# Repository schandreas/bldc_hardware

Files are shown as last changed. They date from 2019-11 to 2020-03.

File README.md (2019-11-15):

This is a fork of Benjamin Vedders Open Source VESC project: https://github.com/vedderb/bldc-hardware

## Goals: 
The original Vesc design is very good for the things it wants to do. I want to do different things and still be able to use the same firmware. So I made this version.

The idea was that I only wanted to drive very weak motors. So this version is cheap and not that good. :man_shrugging:

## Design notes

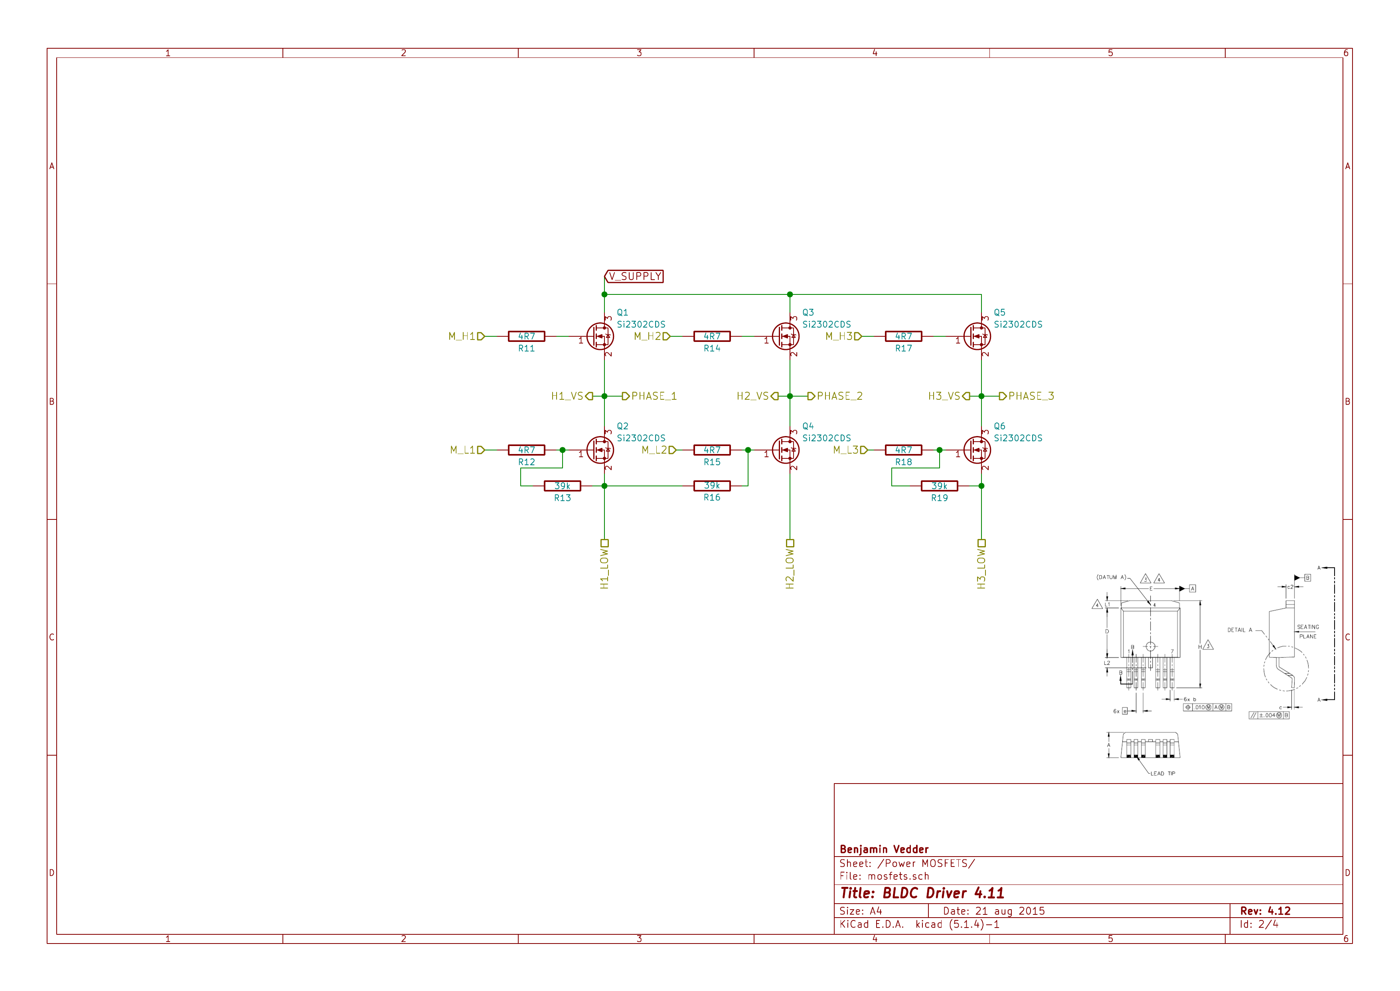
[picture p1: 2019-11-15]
design/PNGs/Schematic-2.png

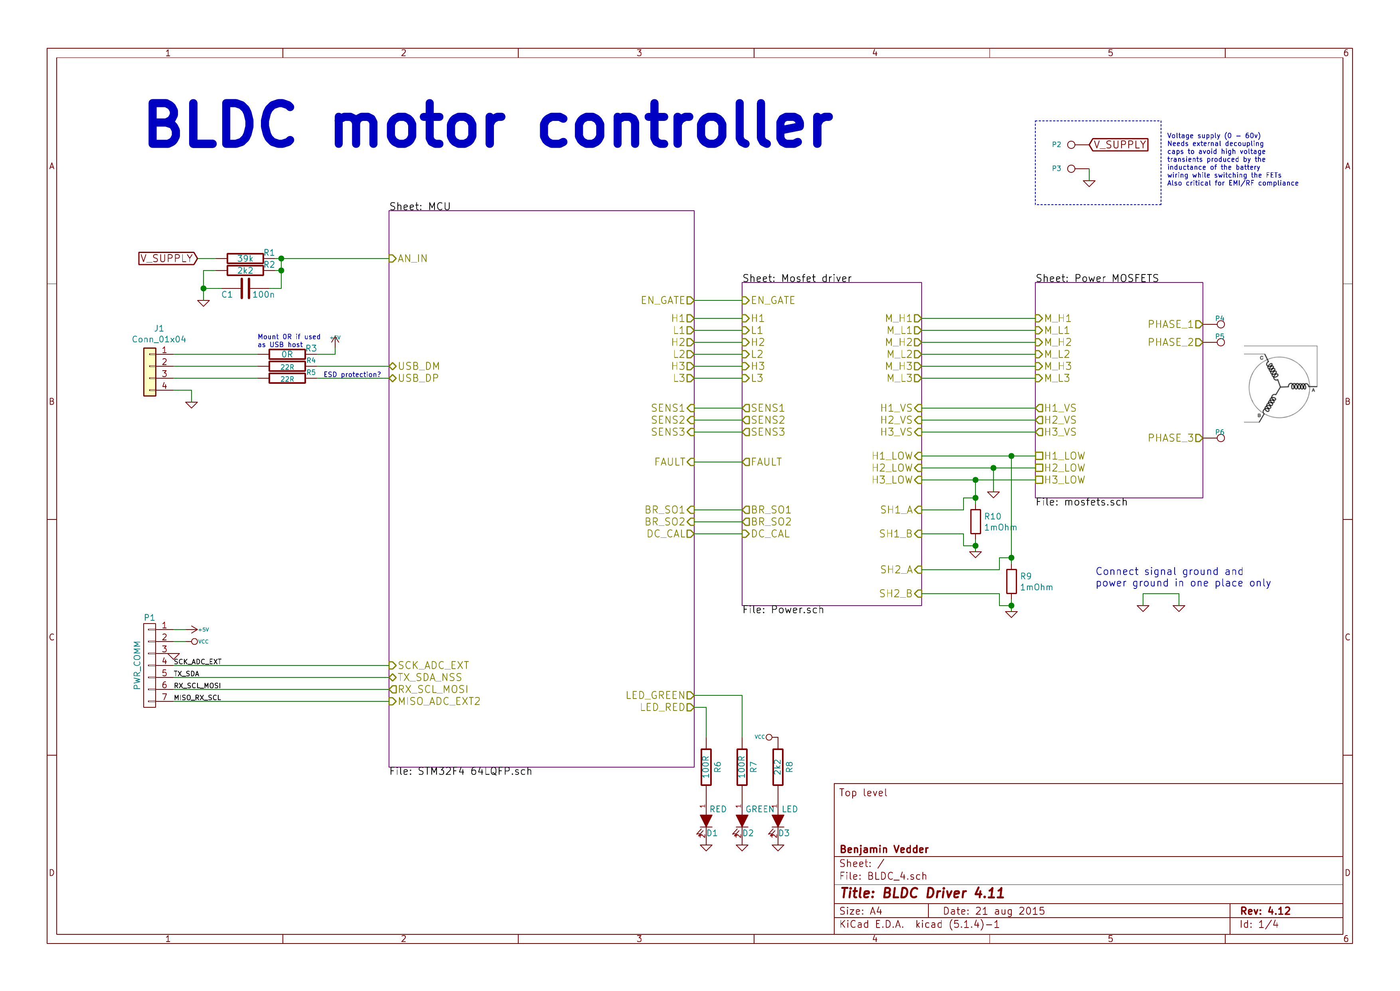
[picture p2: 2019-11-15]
design/PNGs/Schematic-1.png

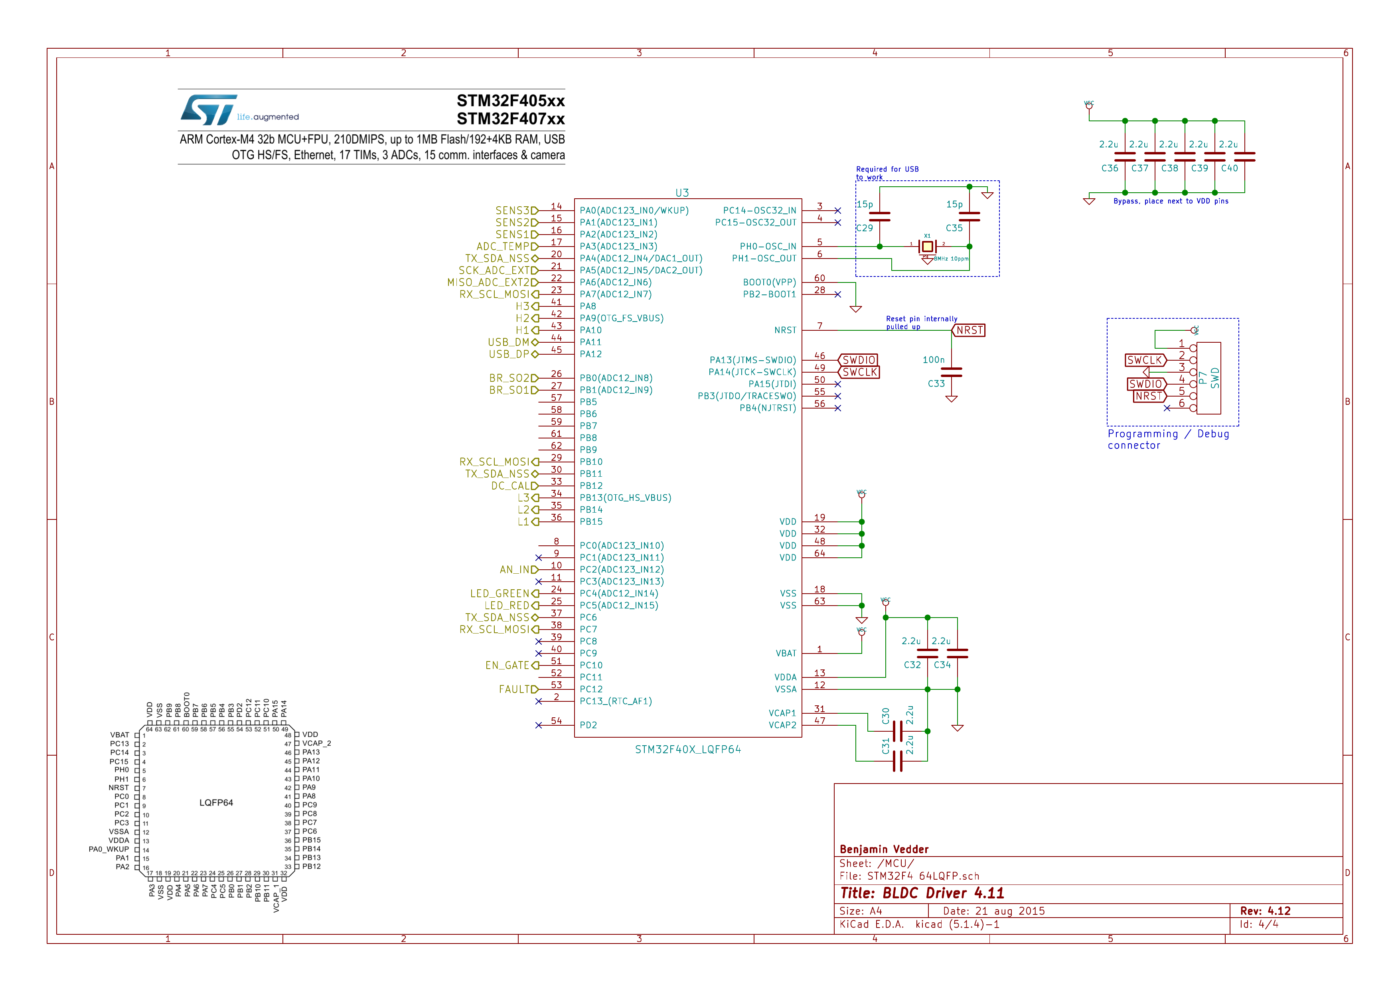
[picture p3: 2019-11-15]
design/PNGs/Schematic-4.png

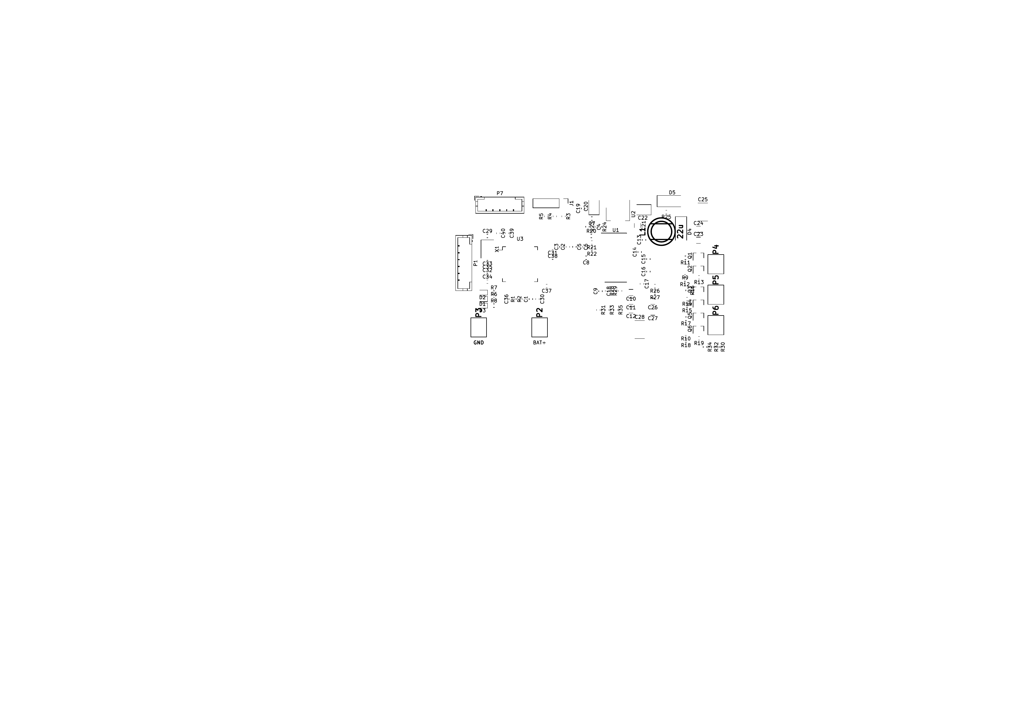
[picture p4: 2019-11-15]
design/PNGs/F_Modules-1.png

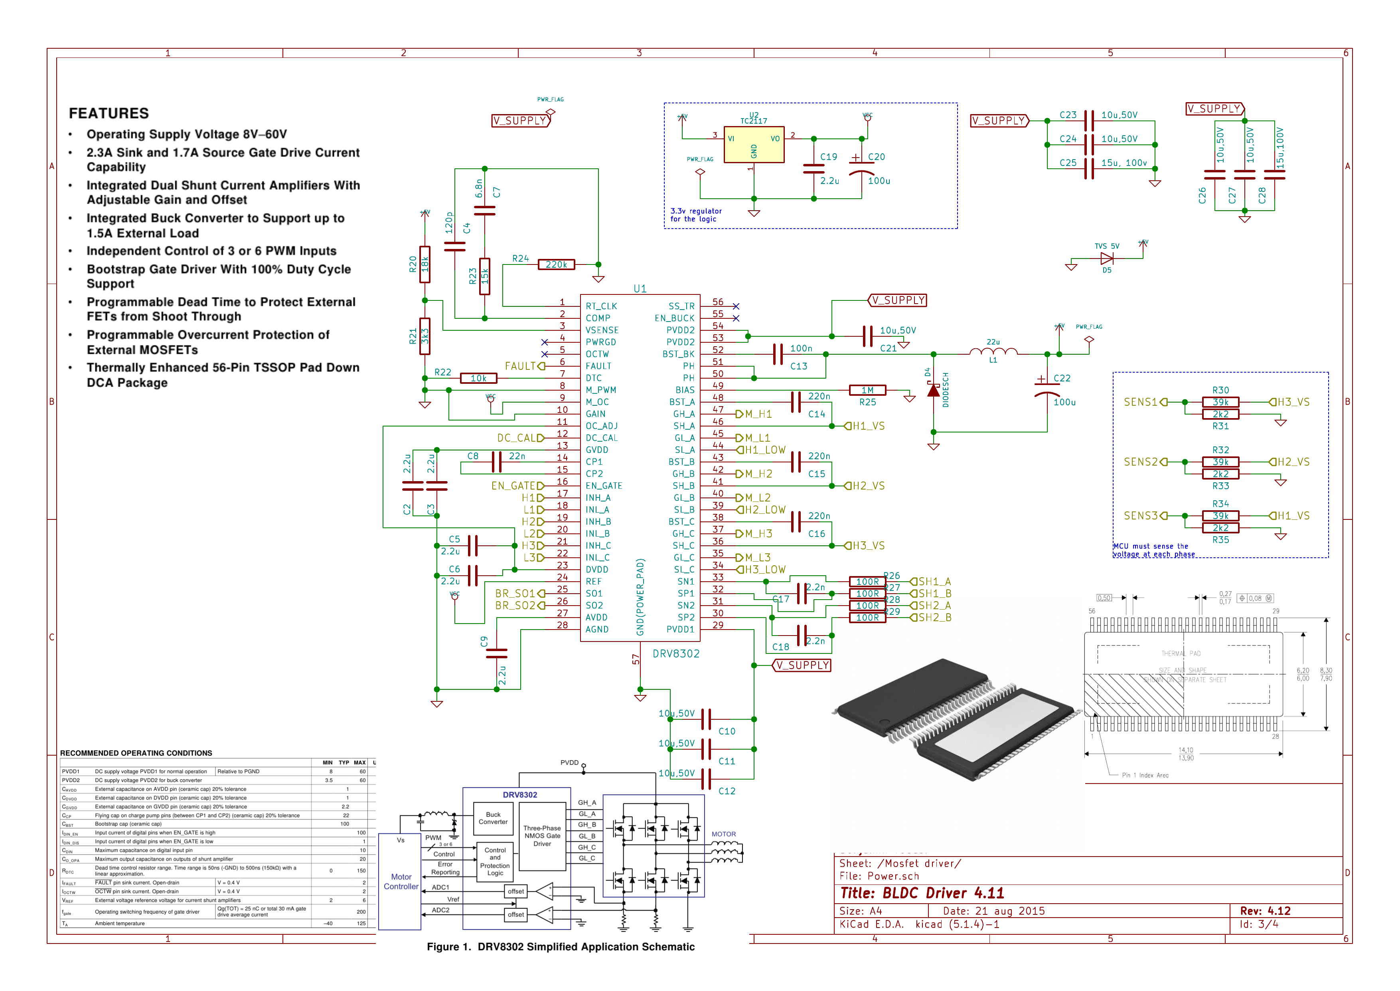
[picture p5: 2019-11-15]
design/PNGs/Schematic-3.png

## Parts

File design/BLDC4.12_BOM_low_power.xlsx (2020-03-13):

Part | Value | Package | Description | Qty | Place (YES/NO) | Distributor | Order Number | Comment | single price | multi price | link | LCSC
U1 |  | LQFP-64 | STM32F405RGT6 MCU | 1 | YES | RS | 746-8217 |  | 9.24 € | 9.24 € | https://at.rs-online.com/web/p/mikrocontroller/7468217/ | https://lcsc.com/product-detail/ST-Microelectronics_STMicroelectronics_STM32F405RGT6_STM32F405RGT6_C15742.html
U2 |  | SOT-223-3 | VREG | 1 | YES | RS | 823-4434 | moq 10 | 0.63 € | 0.63 € | https://at.rs-online.com/web/p/ldo-spannungsregler/8234434/ | https://lcsc.com/product-detail/Low-Dropout-Regulators-LDO_MICROCHIP_TC2117-3-3VDBTR_TC2117-3-3VDBTR_C98655.html
U3 |  | HTSSOP-56-PP | MOSFET Driver | 1 | YES | RS | 762-0421 |  | 5.45 € | 5.45 € | https://at.rs-online.com/web/p/motor-treiber-ics/7620421/ | https://lcsc.com/product-detail/MOS-Drivers_TI_DRV8302DCA_DRV8302DCA_C84672.html
L1 |  | inductor_smd_8x5mm | Power Inductor | 1 | YES | MOUSER | 652-SDR0805-220ML |  | 0.45 € | 0.45 € | https://www.mouser.at/ProductDetail/Bourns/SDR0805-220ML
X1 |  | Conn_1x04 | Pinheader 1x04 2.54mm | 1 | YES | RS | 720-1310 | moq 10 | 0.23 € | 0.23 € | https://at.rs-online.com/web/p/leiterplatten-header/7201310/?sra=pstk
X2 | 8MHz | Crystal_5x3mm | Crystal 8MHz, 10PPM | 1 | YES | MOUSER | 815-ABM3B-8.0-10-1UT |  | 0.62 € | 0.62 € | https://www.mouser.at/ProductDetail/ABRACON/ABM3B-8000MHZ-10-1UT | https://lcsc.com/product-detail/Power-Inductors_BOURNS_SDR0805-220ML_BOURNS-SDR0805-220ML_C139488.html
Q1-Q6 | Si2302CDS | SOT-23 | MOSFET 20V 3A | 6 | YES | Farnell | 1684049 |  | 0.19 € | 1.15 € | https://at.farnell.com/vishay/si2302cds-t1-ge3/mosfet-n-kanal-sot-23/dp/1684049?st=Si2302CDS
R53,R54 | 25mOhm | SMD-0612 | Shunt 25mOhm | 2 | YES | MOUSER | 660-WU732B15TTD25L0F |  | 0.53 € | 1.06 € | https://www.mouser.at/ProductDetail/KOA-Speer/WU732B15TTD25L0F
D5 | 5V | DO-214AC-2 | TVS diode 5V | 1 | YES | MOUSER | 576-SMAJ5.0A |  | 0.37 € | 0.37 € | https://www.mouser.at/ProductDetail/Littelfuse/SMAJ50A
D4 | 60V 2A | SOD-123W-2 | Shottky 60V 2A | 1 | YES | MOUSER | 771-PMEG6020ER-115 | Voltage and current important | 0.32 € | 0.32 € | https://www.mouser.at/ProductDetail/Nexperia/PMEG6020ER115
C25,C33 | 100uF, 6.3V | c_tant_B | CAP 100u, 6.3V | 2 | YES | RS | 136-4122 | Voltage important, moq 25 | 0.44 € | 0.88 € | https://at.rs-online.com/web/p/tantal-elektrolytkondensator/1364122/
C1,C8,C9,C39,C40,C43,C44,C49 | 10uF 50V | SMD1206 | CAP 10u, 50V, 1206 | 8 | YES | MOUSER | 963-UMK316BBJ106ML-T | Voltage important, moq 10 | 0.31 € | 2.48 € | https://www.mouser.at/ProductDetail/Taiyo-Yuden/UMK316BBJ106ML-T
C37,C51 | 15uF, 100V | SMD-2220 | CAP 15u, 100V, 2220 | 2 | YES | MOUSER | 810-CGA9P3X7S2A156M | Voltage important | 3.24 € | 6.48 € | https://www.mouser.at/ProductDetail/TDK/CGA9P3X7S2A156M250KB
C2,C27,C32 | 100nF, 50V | SMD-0603 | CAP 100n, 50V, 0603 | 3 | YES | MOUSER | 581-06035C104JAT2A | Voltage important | 0.14 € | 0.41 € | https://www.mouser.at/ProductDetail/AVX/06035C104JAT2A
C28,C29,C30 | 220nF,25V | SMD-0603 | CAP 220n, 25V, 0603 | 3 | YES | MOUSER | 963-TMK107B7224KA-T | Voltage important | 0.10 € | 0.30 € | https://www.mouser.at/ProductDetail/Taiyo-Yuden/TMK107B7224KA-T
C24,C10,C11,C12,C13,C14,C16,C17,C18,C20,C23,C26,C31,C35,C52 | 2.2uF, 16V | SMD-0603 | CAP 2.2u, 16V, 0603 | 15 | YES | MOUSER | 810-C1608X5R1C225M | Voltage important, moq 10 | 0.17 € | 2.57 € | https://www.mouser.at/ProductDetail/TDK/C1608X5R1C225M080AB
P3 |  | MICRO_JST_7 | Micro-JST 7PIN 2mm | 1 | YES | Conrad | 740103 - 62 | Can be found on ebay (http://www.ebay.com/sch/i.html?_odkw=jst+6+pin+2.0&_osacat=0&_from=R40&_nkw=jst+7+pin+2.0&_sacat=0) | 0.44 € | 0.44 € | https://www.conrad.at/de/p/jst-einbau-stiftleiste-standard-ph-polzahl-gesamt-7-rastermass-2-mm-b7b-ph-k-s-lf-sn-1-st-740103.html | https://lcsc.com/product-detail/Wire-To-Board-Wire-To-Wire-Connector_JST-Sales-America_B7B-PH-K-S-LF-SN_JST-Sales-America-B7B-PH-K-S-LF-SN_C157981.html
P2 |  | MICRO_JST_6 | Micro-JST 6PIN 2mm | 1 | YES | Conrad | 741271 - 62 | Can be found on ebay (http://www.ebay.com/sch/i.html?_odkw=jst+7+pin+2.0&_osacat=0&_from=R40&_nkw=jst+6+pin+2.0&_sacat=0) | 0.69 € | 0.69 € | https://www.conrad.at/de/p/jst-einbau-stiftleiste-standard-ph-polzahl-gesamt-6-rastermass-2-mm-b6b-ph-k-s-lf-sn-1-st-741271.html | https://lcsc.com/product-detail/Wire-To-Board-Wire-To-Wire-Connector_JST-Sales-America_B6B-PH-K-S-LF-SN_JST-Sales-America-B6B-PH-K-S-LF-SN_C131342.html
C34, C36 | 2.2nF, 50V | SMD-0603 | CAP 2.2n, 50V, 0603 | 2 | YES | Farnell | 2409039 | moq 10 | 0.04 € | 0.08 € | https://at.farnell.com/kemet/c0603c222j5ractu/kondensator-2200pf-50v-5-x7r-0603/dp/2409039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 | https://lcsc.com/product-detail/Multilayer-Ceramic-Capacitors-MLCC-SMD-SMT_muRata_GRM188R71H222KA01D_2-2nF-222-10-50V_C86023.html
C15,C38 | 15pF, 100V | SMD-0603 | CAP 15p, 100V, 0603 | 2 | YES | MOUSER | 81-GRM1885C2A150JA01 |  | 0.10 € | 0.20 € | https://www.mouser.at/ProductDetail/Murata-Electronics/GRM1885C2A150JA01D | https://lcsc.com/product-detail/Multilayer-Ceramic-Capacitors-MLCC-SMD-SMT_muRata_GRM1885C2A150JA01D_15pF-150-5-100V_C97715.html
C19 | 120pF, 50V | SMD-0603 | CAP 120p, 50V, 0603 | 1 | YES | MOUSER | 81-GRM39C121J50 |  | 0.14 € | 0.14 € | https://www.mouser.at/ProductDetail/Murata-Electronics/GRM1885C1H121JA01J | https://lcsc.com/product-detail/Multilayer-Ceramic-Capacitors-MLCC-SMD-SMT_Murata-Electronics-GRM1885C1H101JA01J_C415381.html
C21 | 6.8nF, 50V | SMD-0603 | CAP 6.8n, 50V, 0603 | 1 | YES | Farnell | 1759100 | moq 10 | 0.01 € | 0.01 € | https://at.farnell.com/multicomp/mc0603b682k500ct/kondensator-6800pf-50v-10-x7r/dp/1759100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 | https://lcsc.com/product-detail/Multilayer-Ceramic-Capacitors-MLCC-SMD-SMT_MuRata_GRM188R71H682KA01D_6-8nF-682-10-50V_C97896.html
C22 | 22nF, 50V | SMD-0603 | CAP 22n, 50V, 0603 | 1 | YES | Farnell | 1414625 | moq 10 | 0.05 € | 0.05 € | https://at.farnell.com/kemet/c0603c223k5ractu/kondensator-0-022-f-50v-10-x7r/dp/1414625?st=C0603C223K5RACTU | https://lcsc.com/product-detail/Multilayer-Ceramic-Capacitors-MLCC-SMD-SMT_KEMET_C0603C223K5RAC7867_22nF-223-10-50V_C141095.html
D1 |  | SMD-0603 | LED Green, 0603 | 1 | YES | MOUSER | 859-LTST-C191KGKT |  | 0.23 € | 0.23 € | https://www.mouser.at/ProductDetail/Lite-On/LTST-C191KGKT | https://lcsc.com/product-detail/Light-Emitting-Diodes-LED_SMD-green_C125098.html
D2 |  | SMD-0603 | LED Red, 0603 | 1 | YES | MOUSER | 859-LTST-C191KRKT |  | 0.23 € | 0.23 € | https://www.mouser.at/ProductDetail/Lite-On/LTST-C191KRKT | https://lcsc.com/product-detail/Light-Emitting-Diodes-LED_SMD-red_C125099.html
D3 |  | SMD-0603 | LED Blue, 0603 | 1 | YES | MOUSER | 720-LBQ39GN1P1351 |  | 0.39 € | 0.39 € | https://www.mouser.at/ProductDetail/OSRAM-Opto-Semiconductors/LB-Q39G-N1OO-35-1
R28,R29,R34,R35,R42,R43 | 4.7ohm | SMD-0603 | R 4.7ohm, 0603 | 6 | YES | MOUSER | 660-RK73H1JTTD4R70F | moq 10 | 0.02 € | 0.13 € | https://www.mouser.at/ProductDetail/KOA-Speer/RK73H1JTTD4R70F | https://lcsc.com/product-detail/Chip-Resistor-Surface-Mount_KOA-Speer-Elec-RK73H1JTTD4R70F_C211717.html
R37,R38,R48-R51,R401 | 100ohm | SMD-0603 | R 100ohm, 0603 | 6 | YES | Farnell | 2074165 | moq 10 | 0.01 € | 0.06 € | https://at.farnell.com/multicomp/mcsr06x1000ftl/keramikwiderstand-100r-1-0-1w/dp/2074165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 | https://lcsc.com/product-detail/Chip-Resistor-Surface-Mount_100R-100R-1_C139043.html
R4,R5,R11,R12,R13,R22,R24,R27,R33 | 2.2kOhm | SMD-0603 | R 2.2k, 0603 | 5 | YES | Farnell | 2074215 | moq 10 | 0.01 € | 0.05 € | https://at.farnell.com/multicomp/mcsr06x2201ftl/keramikwiderstand-2k2-1-0-1w-0603/dp/2074215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 | https://lcsc.com/product-detail/Chip-Resistor-Surface-Mount_2-2KR-2201-1_C130233.html
R18 | 3.3kOhm | SMD-0603 | R 3.3k, 0603 | 1 | YES | MOUSER | 660-RK73H1JTTD3301F |  | 0.10 € | 0.10 € | https://www.mouser.at/ProductDetail/KOA-Speer/RK73H1JTTD3301F | https://lcsc.com/product-detail/Chip-Resistor-Surface-Mount_3-3KR-3301-1_C160039.html
R20 | 10kOhm | SMD-0603 | R 10k, 0603 | 1 | YES | Farnell | 2074167 | moq 10 | 0.01 € | 0.01 € | https://at.farnell.com/multicomp/mcsr06x1002ftl/keramikwiderstand-10k-1-0-1w-0603/dp/2074167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 | https://lcsc.com/product-detail/Chip-Resistor-Surface-Mount_10KR-1002-1_C130232.html
R19 | 15kOhm | SMD-0603 | R 15k, 0603 | 1 | YES | MOUSER | 660-RK73H1JTTD1502F |  | 0.10 € | 0.10 € | https://www.mouser.at/ProductDetail/KOA-Speer/RK73H1JTTD1502F | https://lcsc.com/product-detail/Chip-Resistor-Surface-Mount_15KR-1502-1_C160018.html
R17 | 18kOhm | SMD-0603 | R 18k, 0603 | 1 | YES | Farnell | 2074204 |  | 0.01 € | 0.01 € | https://at.farnell.com/multicomp/mcsr06x1802ftl/keramikwiderstand-18k-1-0-1w-0603/dp/2074204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 | https://lcsc.com/product-detail/Chip-Resistor-Surface-Mount_18KR-1802-1_C211701.html
R3,R23,R26,R30,R32,R36,R46 | 39kOhm | SMD-0603 | R 39k, 0603 | 7 | YES | Farnell | 2303209 | moq 10 | 0.02 € | 0.11 € | https://at.farnell.com/panasonic/erj3ekf3902v/dickschichtwiderstand-39k-1-100mw/dp/2303209?st=ERJ-3EKF3902V | https://lcsc.com/product-detail/Chip-Resistor-Surface-Mount_PANASONIC-ERJ3EKF3902V_C278624.html
R21 | 220kOhm | SMD-0603 | R 220k, 0603 | 1 | YES | MOUSER | 660-RK73H1JTTD2203F |  | 0.10 € | 0.10 € | https://www.mouser.at/ProductDetail/KOA-Speer/RK73H1JTTD2203F | https://lcsc.com/product-detail/Others_KOA-Speer-Elec-RK73H1JTTD2203F_C268814.html
R25 | 1MOhm | SMD-0603 | R 1M, 0603 | 1 | YES | MOUSER | 660-RK73H1JTTD1004F |  | 0.10 € | 0.10 € | https://www.mouser.at/ProductDetail/KOA-Speer/RK73H1JTTD1004F | https://lcsc.com/product-detail/Chip-Resistor-Surface-Mount_1MR-1004-1_C139051.html
R103, R104 | 22ohm | SMD-0603 | R 22R, 0603 | 2 | YES | Farnell | 2074219 | moq 10 | 0.01 € | 0.03 € | https://at.farnell.com/multicomp/mcsr06x22r0ftl/keramikwiderstand-22r-1-0-1w-0603/dp/2074219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 | https://lcsc.com/product-detail/Chip-Resistor-Surface-Mount_22R-22R0-1_C160030.html
R6 |  |  |  | 0 | NO |  |  | Do not mount |  | 0.00 €
1PIN,1PIN |  |  |  | 0 | NO |  |  | Do not mount |  | 0.00 €
K1 |  |  |  | 0 | NO |  |  | Do not mount |  | 0.00 €
P5,P5,P6,P7,P9 |  |  |  | 0 | NO |  |  | Do not mount |  | 0.00 €
G*** |  |  |  | 0 | NO |  |  | Do not mount |  | 0.00 €
 |  |  |  |  |  |  |  |  |  | 35.88 €
 |  |  |  | 20 |  | RS | · 820-1412 | moq 10-40 | 0.60 € |  | https://at.rs-online.com/web/p/konfektionierte-automationskabel/8201412/
 |  |  |  | 10 |  | RS | · 820-1481 | moq 10-490 | 0.10 € |  | https://at.rs-online.com/web/p/leiterplattensteckverbinder-gehause/8201481/
 |  |  |  | 10 |  | RS | · 820-1478 | moq 10-490 | 0.08 € |  | https://at.rs-online.com/web/p/leiterplattensteckverbinder-gehause/8201478/
 |  |  |  | 100 |  | RS | · 820-1456 | moq 100-900 | 0.03 € |  | https://at.rs-online.com/web/p/kontakte-fur-leiterplattensteckverbinder/8201456/

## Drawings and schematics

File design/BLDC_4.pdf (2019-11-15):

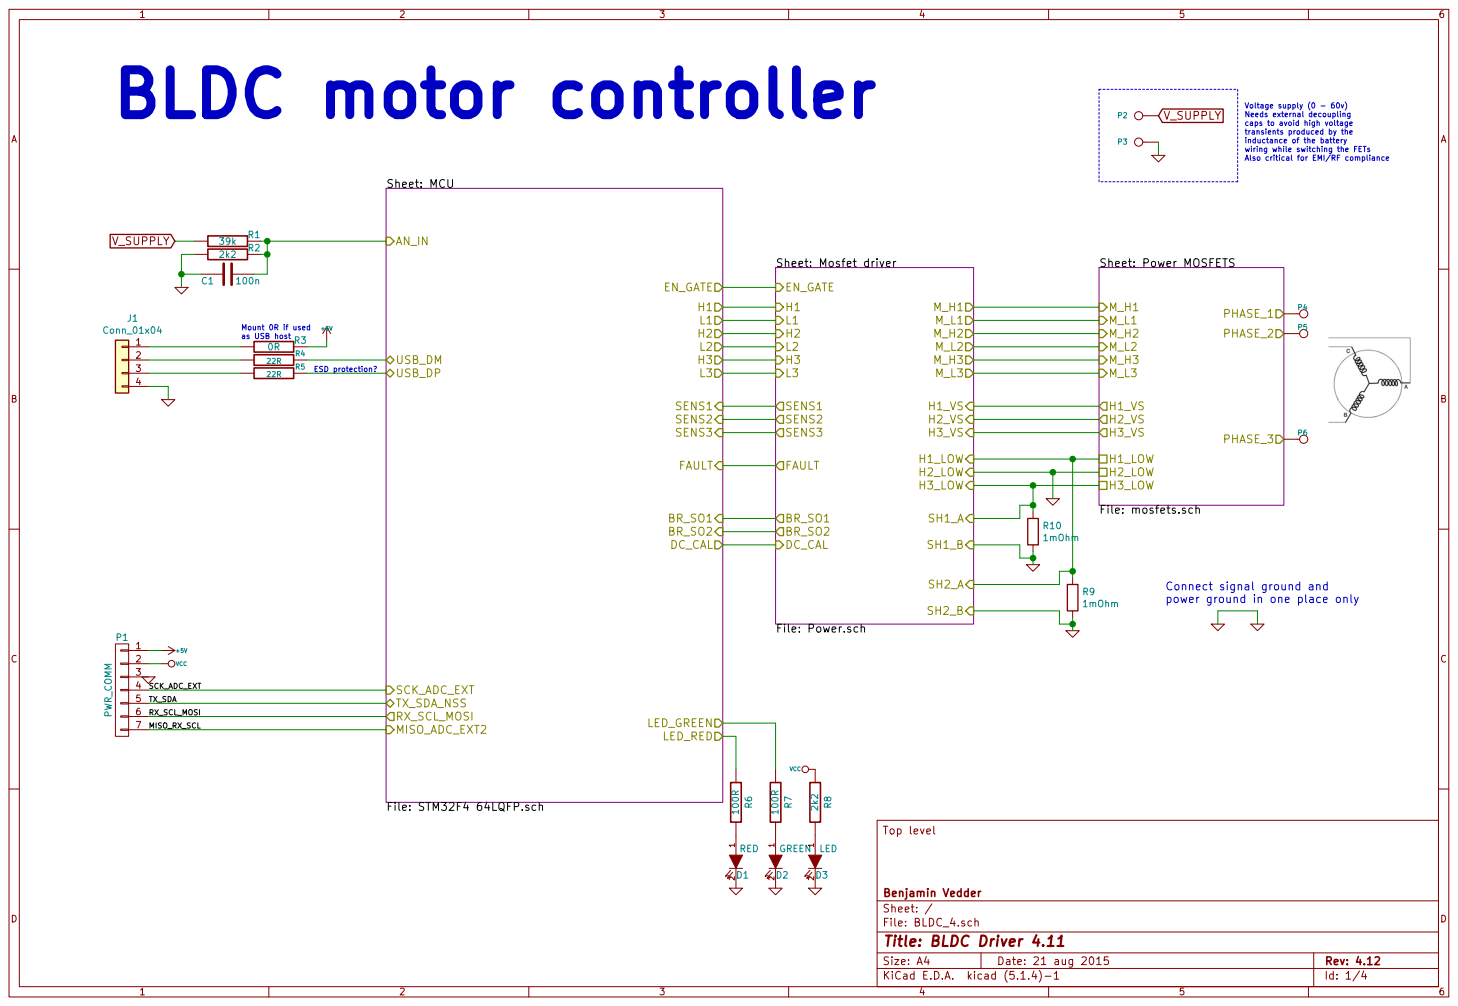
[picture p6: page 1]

inductance of the battery wiring while switching the FETs Also critical for EMI/RF compliance BLDC motor controller

Voltage supply (0 - 60v) Needs external decoupling

caps to avoid high voltage
transients produced by the

ESD protection? Mount 0R if used

power ground in one place only

File: BLDC_4.sch Sheet: / Benjamin Vedder

Id: 1/4 Title: BLDC Driver 4.11

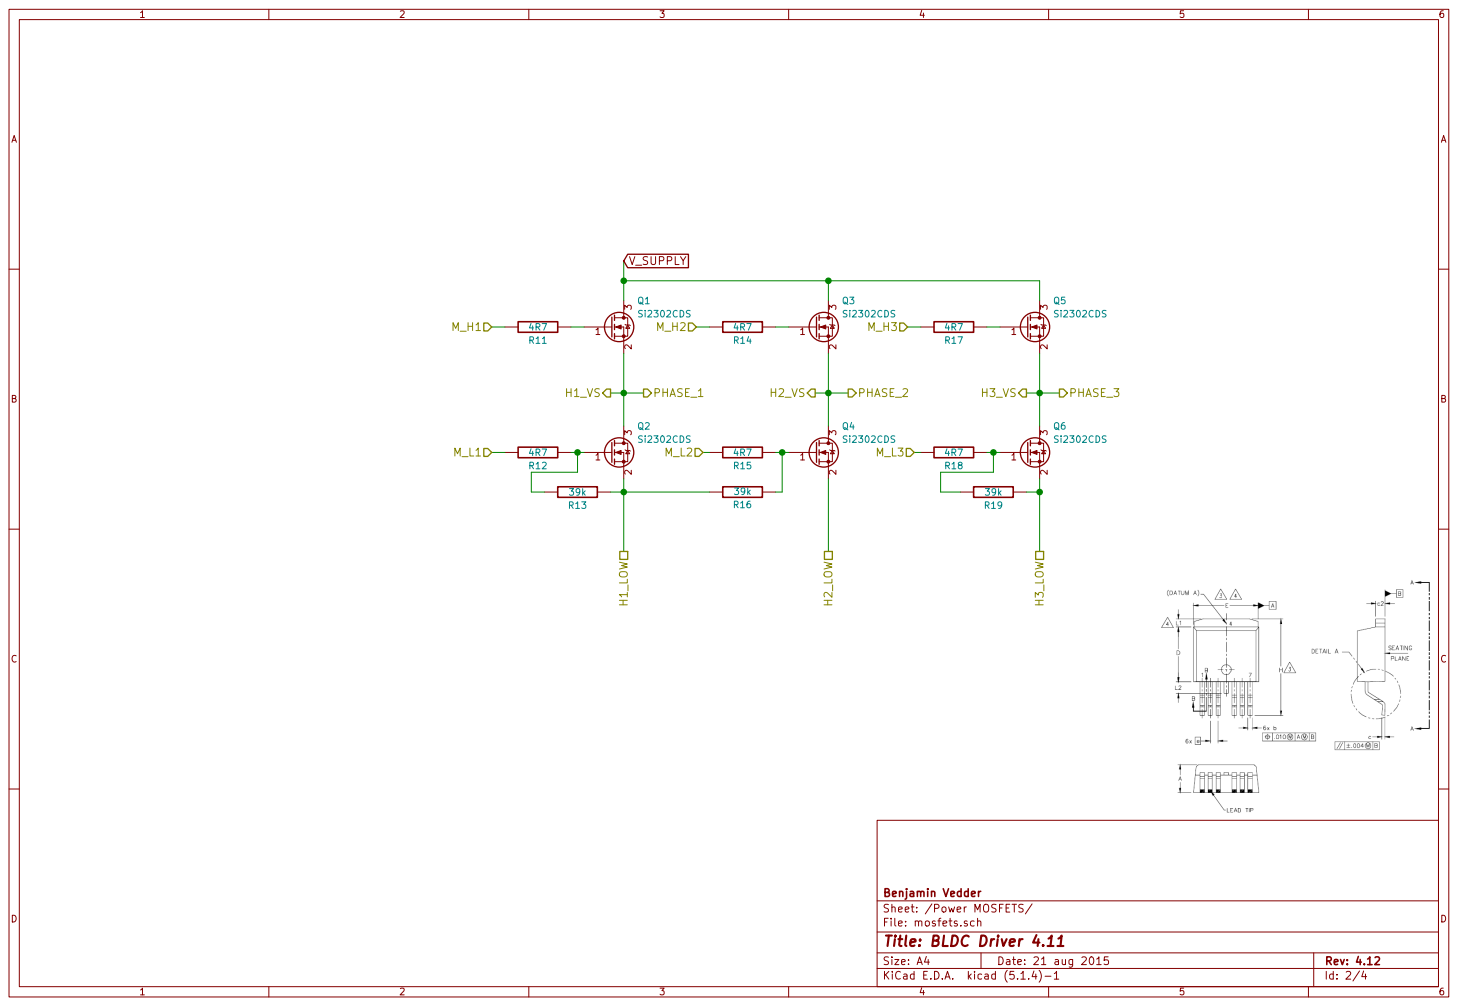
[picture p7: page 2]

File: mosfets.sch Sheet: /Power MOSFETS/ Benjamin Vedder R13

Id: 2/4 Title: BLDC Driver 4.11

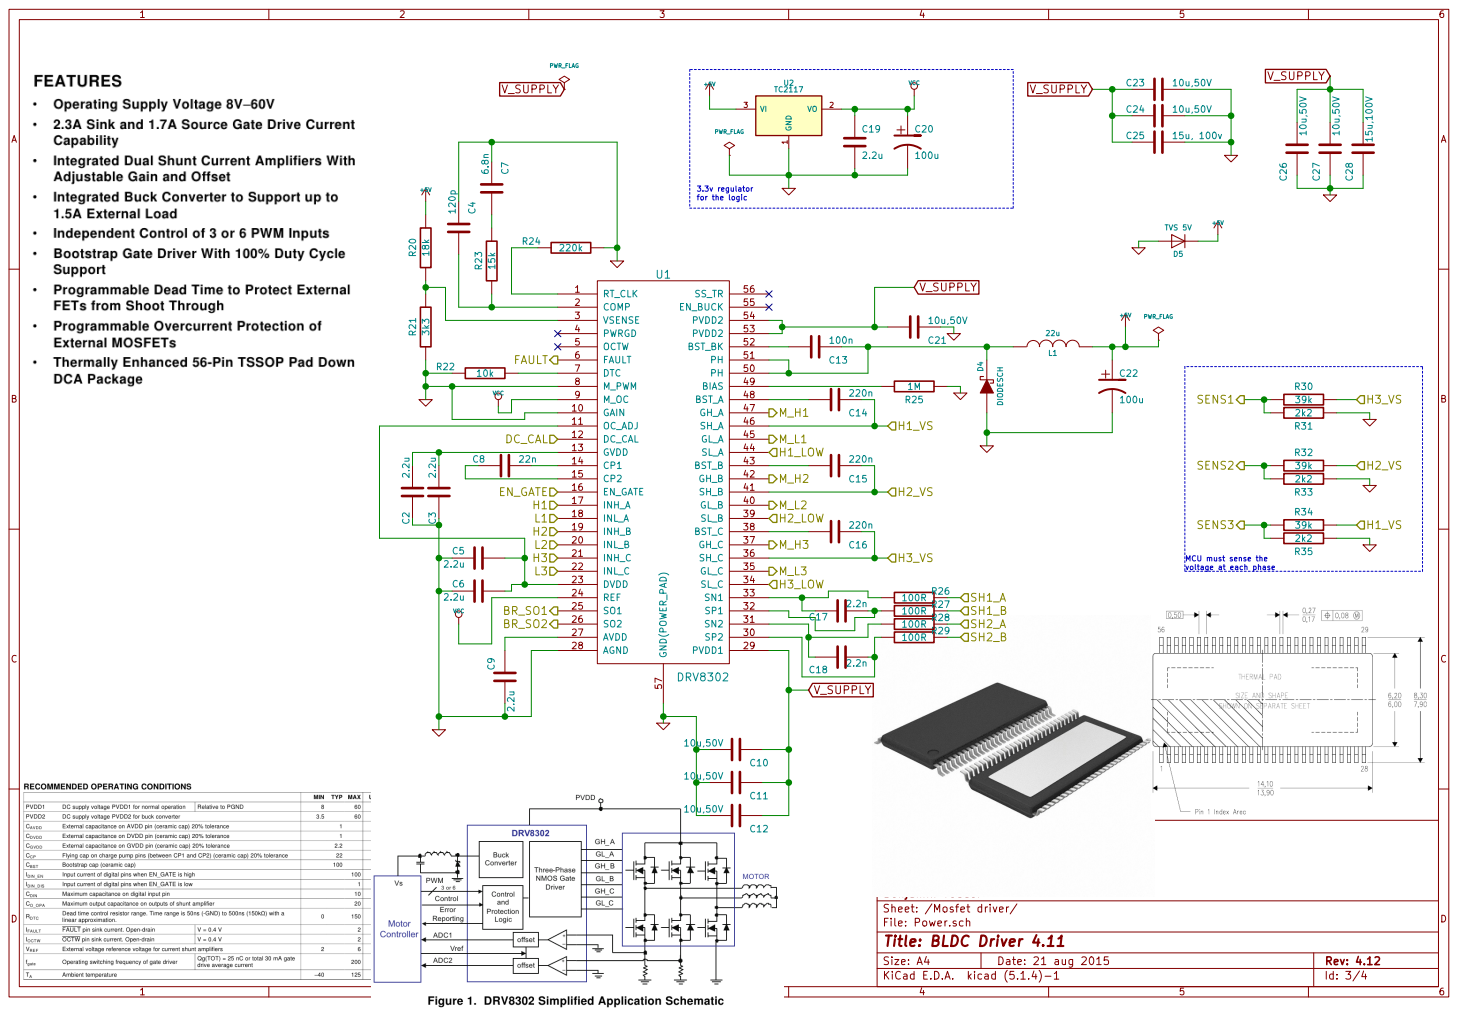
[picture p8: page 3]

MCU must sense the
voltage at each phase

File: Power.sch Sheet: /Mosfet driver/ Benjamin Vedder

Id: 3/4 Title: BLDC Driver 4.11

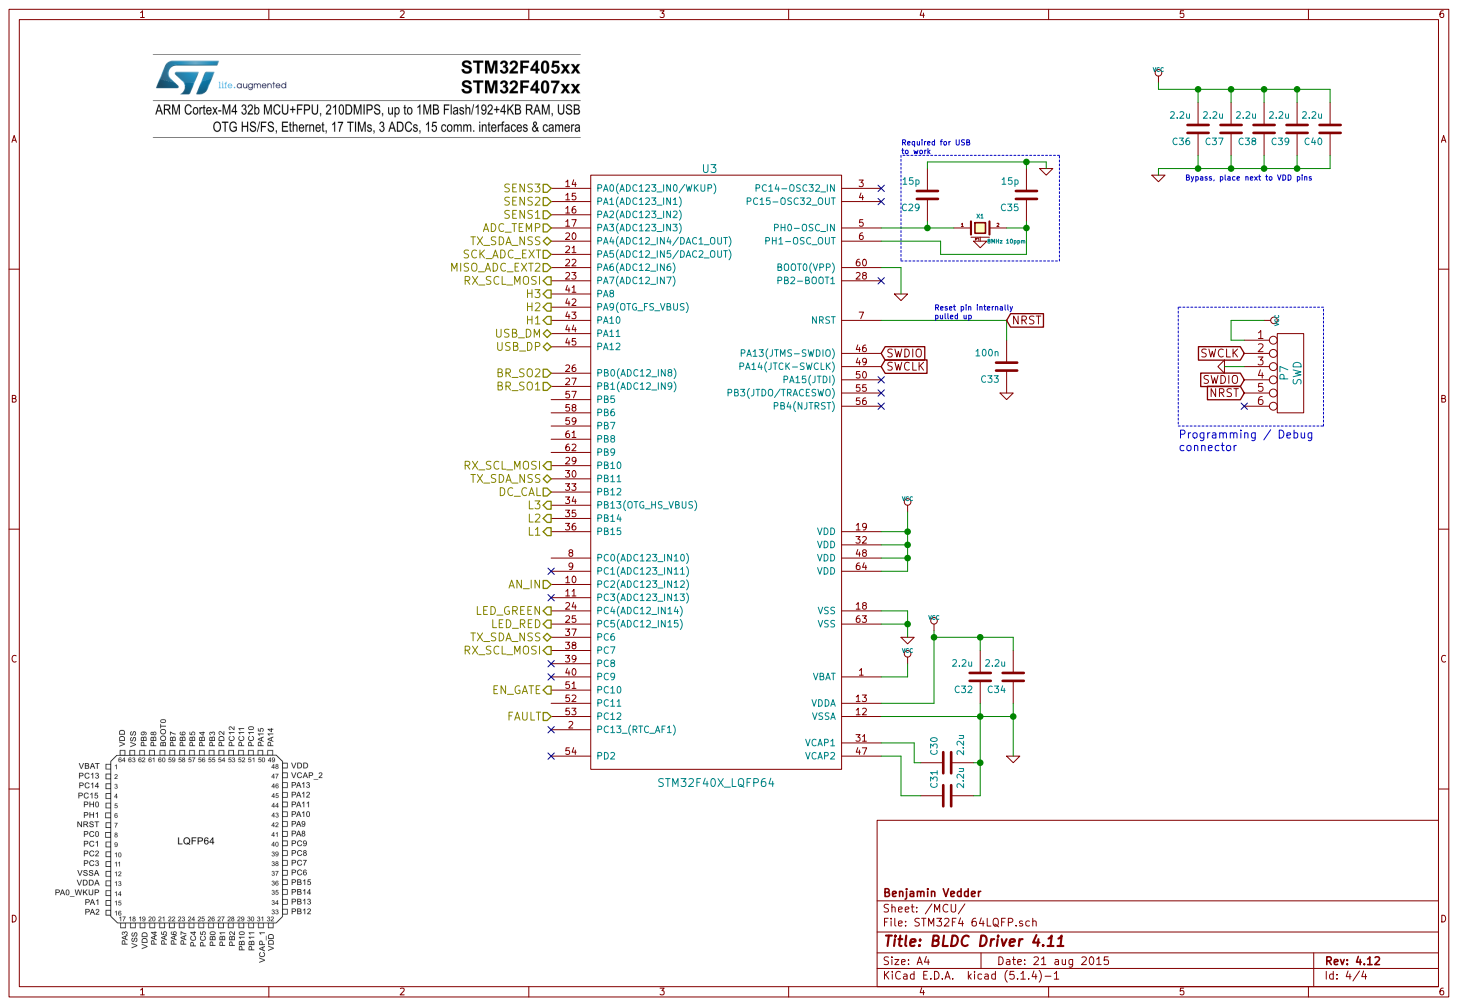
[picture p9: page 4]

connector Bypass, place next to VDD pins

Reset pin internally pulled up Required for USB

Id: 4/4 Title: BLDC Driver 4.11

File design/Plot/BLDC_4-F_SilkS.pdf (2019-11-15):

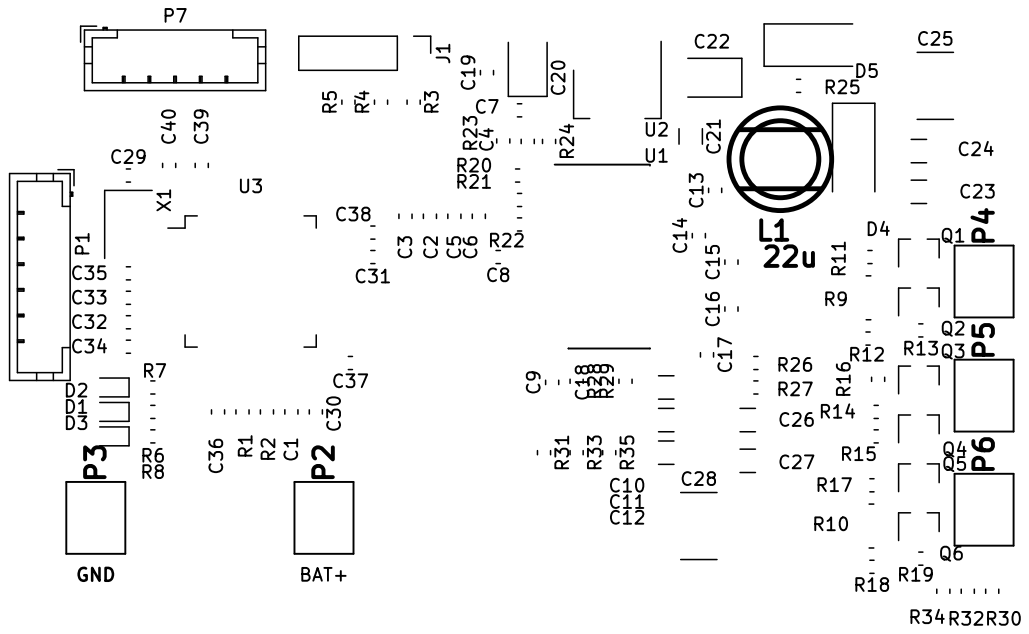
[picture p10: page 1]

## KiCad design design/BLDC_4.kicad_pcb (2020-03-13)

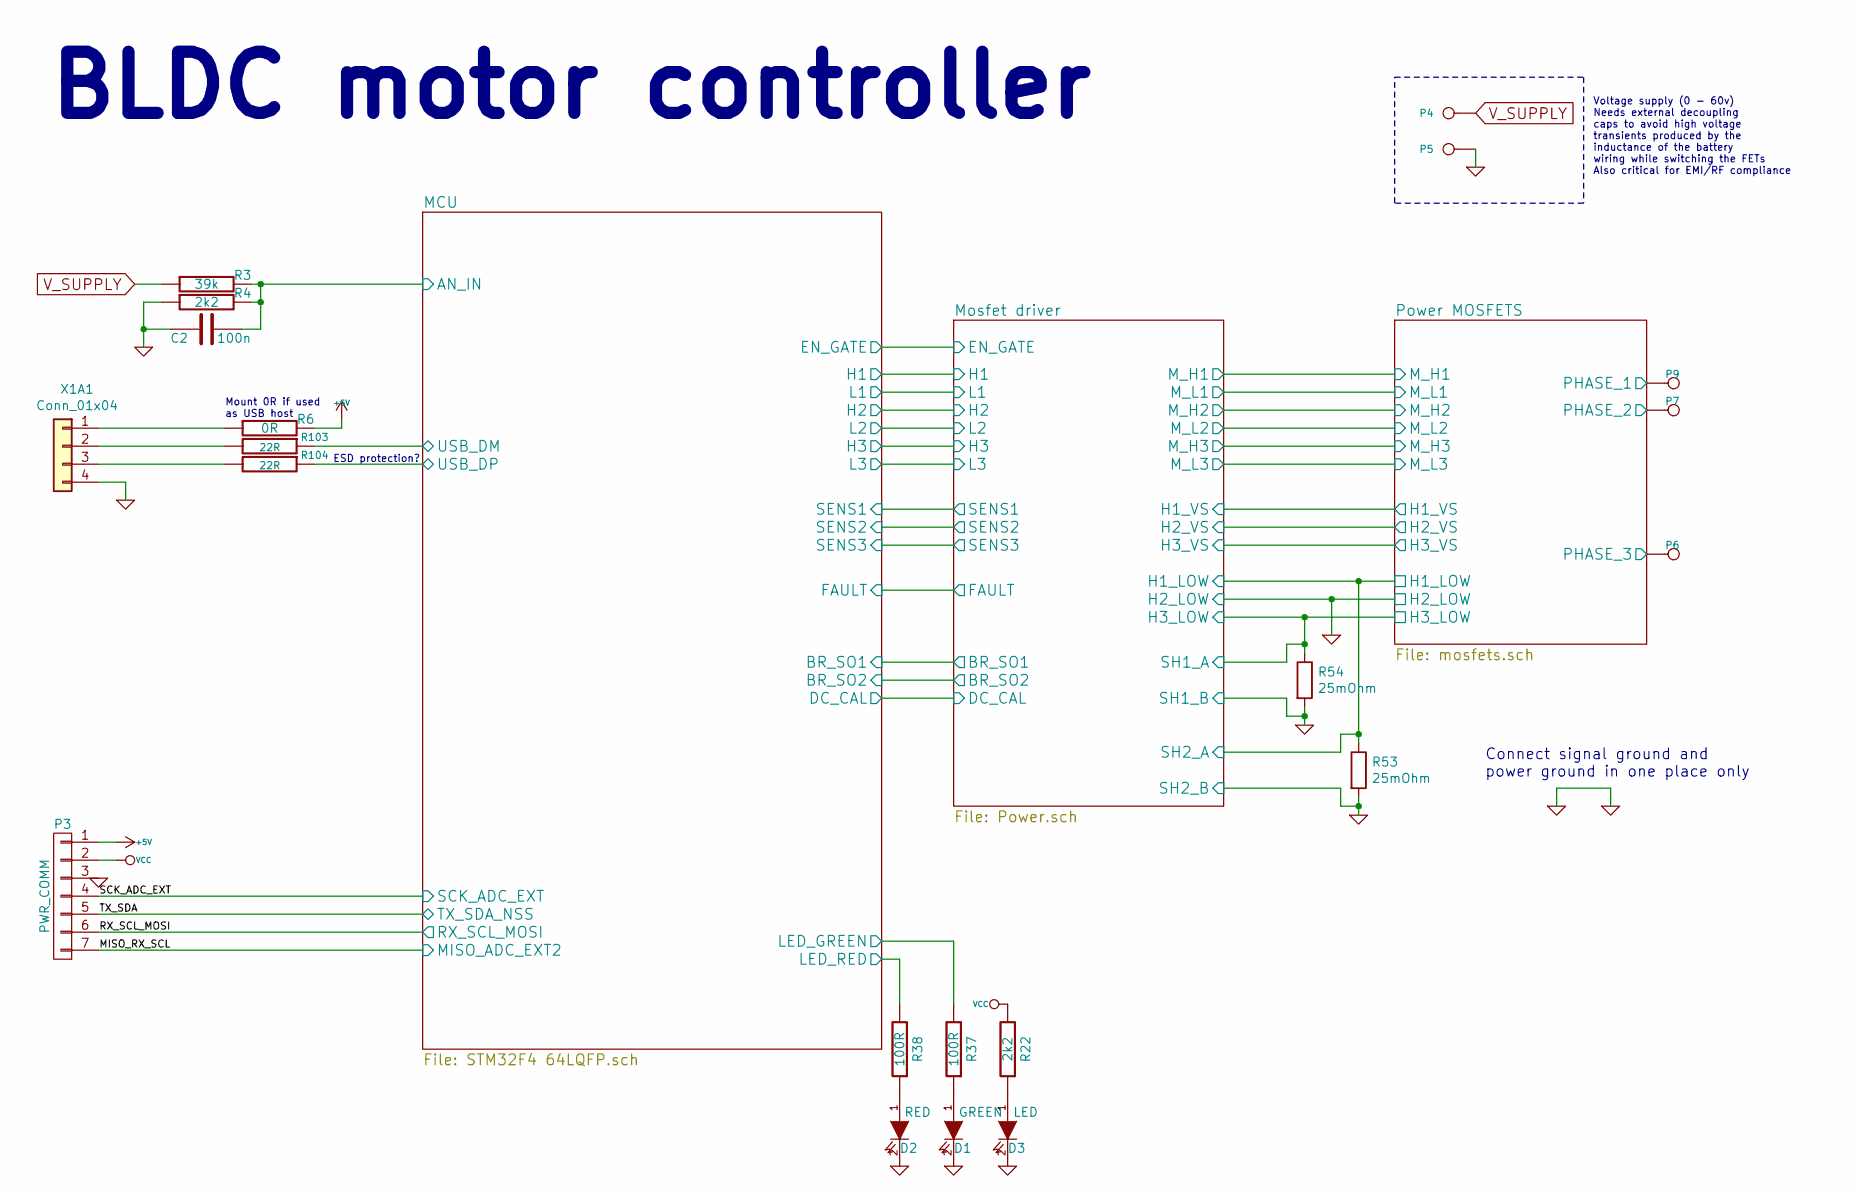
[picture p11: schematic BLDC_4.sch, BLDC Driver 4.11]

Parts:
C2: 100n; C_0603_1608Metric_Pad1.05x0.95mm_HandSolder
D1: GREEN; LED_0603_1608Metric
D2: RED; LED_0603_1608Metric
D3: LED; LED_0603_1608Metric
P3: PWR_COMM; JST_PH_B7B-PH-K_1x07_P2.00mm_Vertical
P4: IN+; 1PAD_4x5mm
P5: IN-; 1PAD_4x5mm
P6: MOTOR1; 1PAD_4x5mm
P7: MOTOR2; 1PAD_4x5mm
P9: MOTOR3; 1PAD_4x5mm
R3: 39k; R_0603_1608Metric
R4, R22: 2k2; R_0603_1608Metric
R6: 0R; R_0603_1608Metric
R37, R38: 100R; R_0603_1608Metric
R53, R54: 25mOhm; R_0612_1632Metric
R103, R104: 22R; R_0603_1608Metric
X1A1: Conn_01x04; PinHeader_1x04_P2.54mm_Vertical

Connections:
+5V: P3.1, R6.2; also elsewhere on the board
/MCU/AN_IN: C2.2, R3.2, R4.2; also elsewhere on the board
/MCU/LED_GREEN: R37.2; also elsewhere on the board
/MCU/LED_RED: R38.2; also elsewhere on the board
/MCU/USB_DM: R103.1; also elsewhere on the board
/MCU/USB_DP: R104.1; also elsewhere on the board
/MISO_RX_SCL: P3.7; also elsewhere on the board
/Mosfet driver/H1_LOW: R53.1; also elsewhere on the board
/Mosfet driver/H1_VS: P9.1; also elsewhere on the board
/Mosfet driver/H2_VS: P7.1; also elsewhere on the board
/Mosfet driver/H3_LOW: R54.1; also elsewhere on the board
/Mosfet driver/H3_VS: P6.1; also elsewhere on the board
/RX_SCL_MOSI: P3.6; also elsewhere on the board
/SCK_ADC_EXT: P3.4; also elsewhere on the board
/TX_SDA: P3.5; also elsewhere on the board
GND: C2.1, D1.2 (K), D2.2 (K), D3.2 (K), P3.3, P5.1, R4.1, R53.2, R54.2, X1A1.4; also elsewhere on the board
unnamed: D1.1 (A), R37.1
unnamed: D2.1 (A), R38.1
unnamed: D3.1 (A), R22.1
unnamed: R6.1, X1A1.1
unnamed: R103.2, X1A1.2
unnamed: R104.2, X1A1.3
VCC: P3.2, R22.2; also elsewhere on the board
V_SUPPLY: P4.1, R3.1; also elsewhere on the board

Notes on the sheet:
Mount 0R if used as USB host
ESD protection?
BLDC motor controller
Voltage supply (0 - 60v) Needs external decoupling caps to avoid high voltage transients produced by the inductance of the battery wiring while switching the FETs Also critical for EMI/RF compliance
Connect signal ground and power ground in one place only

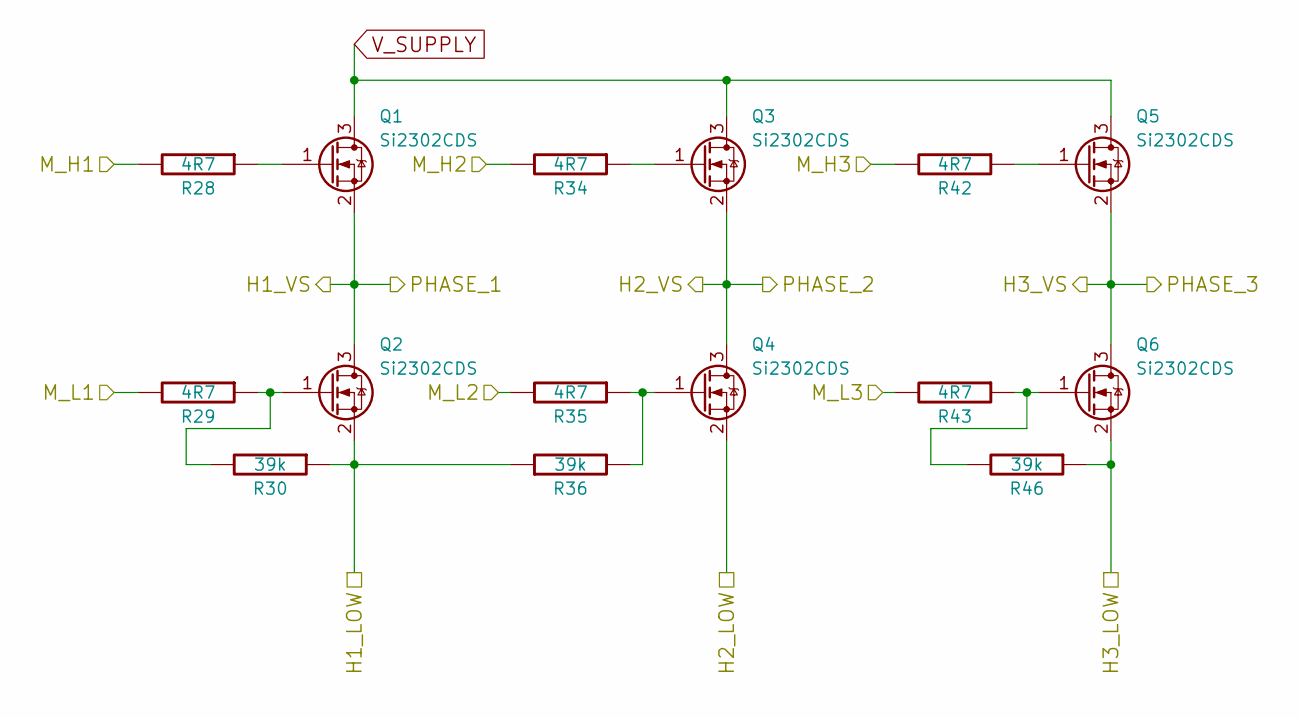
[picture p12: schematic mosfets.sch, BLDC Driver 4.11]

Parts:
Q1, Q2, Q3, Q4, Q5, Q6: Si2302CDS; SOT-23
R28, R29, R34, R35, R42, R43: 4R7; R_0603_1608Metric
R30, R36, R46: 39k; R_0603_1608Metric

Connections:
/Mosfet driver/H1_LOW: Q2.2 (S), R30.1, R36.1; also elsewhere on the board
/Mosfet driver/H1_VS: Q1.2 (S), Q2.3 (D); also elsewhere on the board
/Mosfet driver/H2_VS: Q3.2 (S), Q4.3 (D); also elsewhere on the board
/Mosfet driver/H3_LOW: Q6.2 (S), R46.1; also elsewhere on the board
/Mosfet driver/H3_VS: Q5.2 (S), Q6.3 (D); also elsewhere on the board
/Mosfet driver/M_H1: R28.2; also elsewhere on the board
/Mosfet driver/M_H2: R34.2; also elsewhere on the board
/Mosfet driver/M_H3: R42.2; also elsewhere on the board
/Mosfet driver/M_L1: R29.2; also elsewhere on the board
/Mosfet driver/M_L2: R35.2; also elsewhere on the board
/Mosfet driver/M_L3: R43.2; also elsewhere on the board
GND: Q4.2 (S); also elsewhere on the board
unnamed: Q1.1 (G), R28.1
unnamed: Q2.1 (G), R29.1, R30.2
unnamed: Q3.1 (G), R34.1
unnamed: Q4.1 (G), R35.1, R36.2
unnamed: Q5.1 (G), R42.1
unnamed: Q6.1 (G), R43.1, R46.2
V_SUPPLY: Q1.3 (D), Q3.3 (D), Q5.3 (D); also elsewhere on the board

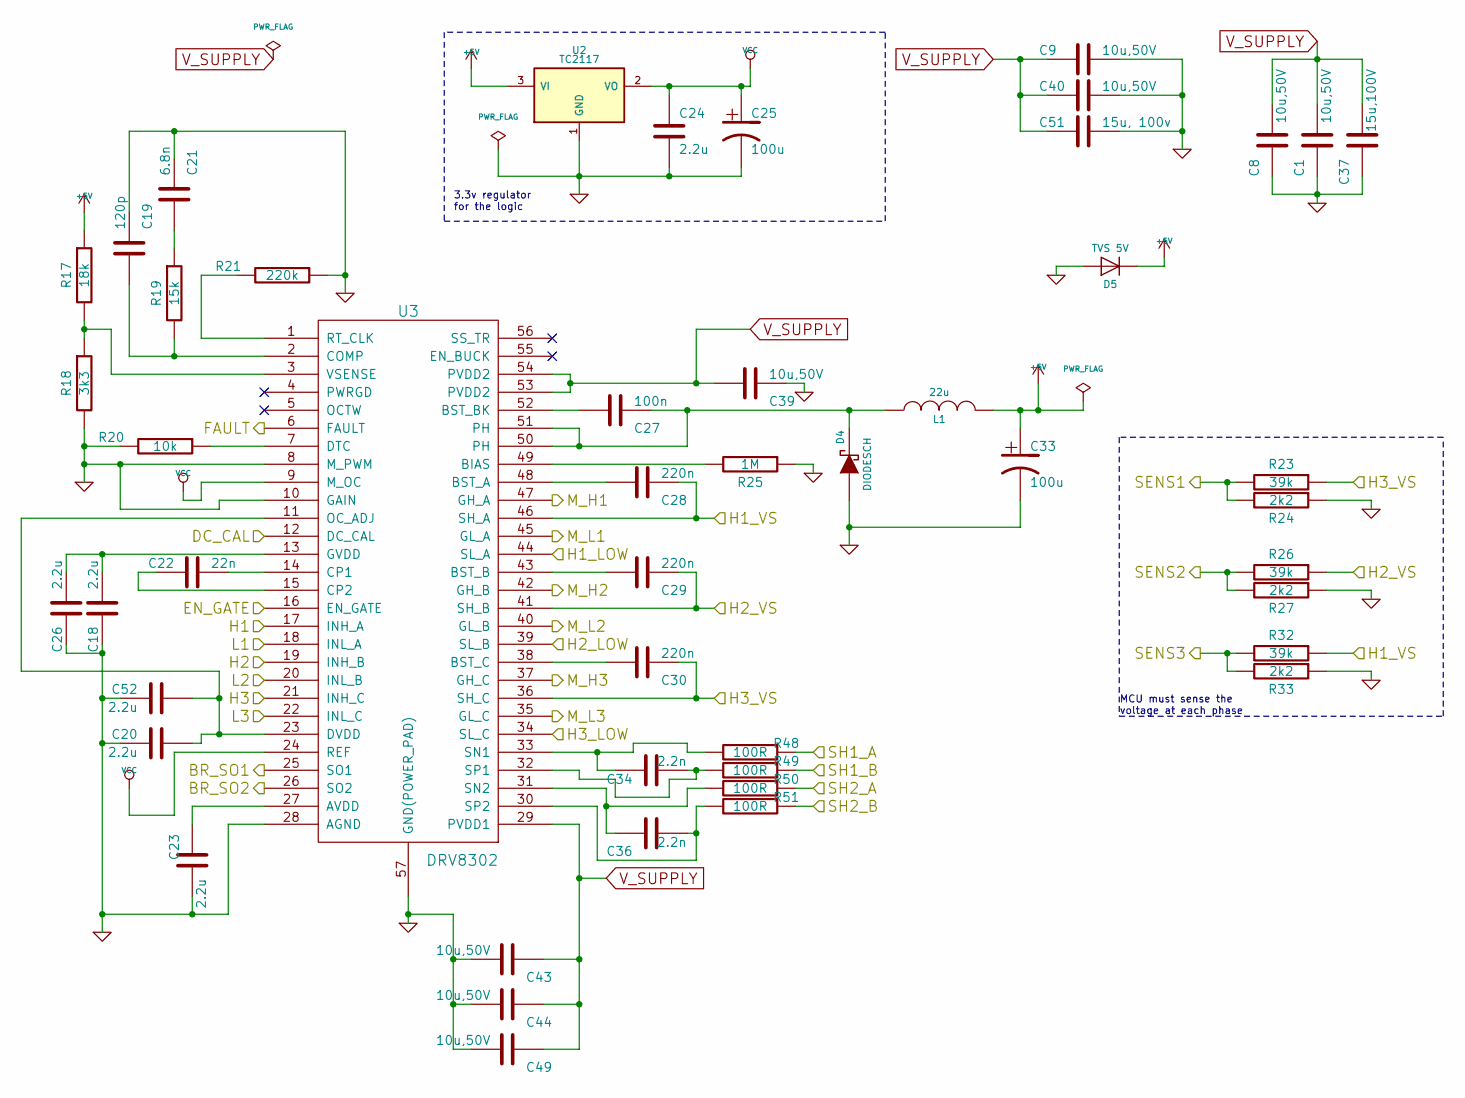
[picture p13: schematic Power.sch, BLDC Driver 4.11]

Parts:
C1, C8, C9, C39, C40, C43, C44, C49: 10u,50V; C_1206_3216Metric
C18, C20, C23, C24, C26, C52: 2.2u; C_0603_1608Metric_Pad1.05x0.95mm_HandSolder
C19: 120p; C_0603_1608Metric_Pad1.05x0.95mm_HandSolder
C21: 6.8n; C_0603_1608Metric_Pad1.05x0.95mm_HandSolder
C22: 22n; C_0603_1608Metric_Pad1.05x0.95mm_HandSolder
C25, C33: 100u; CP_EIA-3528-21_Kemet-B
C27: 100n; C_0603_1608Metric_Pad1.05x0.95mm_HandSolder
C28, C29, C30: 220n; C_0603_1608Metric_Pad1.05x0.95mm_HandSolder
C34, C36: 2.2n; C_0603_1608Metric_Pad1.05x0.95mm_HandSolder
C37: 15u,100V; C_2220_5650Metric
C51: 15u, 100v; C_2220_5650Metric
D4: DIODESCH; D_SMA_Handsoldering
D5: TVS 5V; D_SMA_Handsoldering
L1: 22u; inductor_smd_8x5mm
R17: 18k; R_0603_1608Metric
R18: 3k3; R_0603_1608Metric
R19: 15k; R_0603_1608Metric
R20: 10k; R_0603_1608Metric
R21: 220k; R_0603_1608Metric
R23, R26, R32: 39k; R_0603_1608Metric
R24, R27, R33: 2k2; R_0603_1608Metric
R25: 1M; R_0603_1608Metric
R48, R49, R50, R51: 100R; R_0603_1608Metric
U2: TC2117; SOT-223-3_TabPin2
U3: DRV8302; HTSSOP-56-1EP_6.1x14mm_P0.5mm_EP3.61x6.35mm

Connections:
+5V: C33.1, D5.1 (K), L1.2, R17.1, U2.3 (VI); also elsewhere on the board
/MCU/BR_SO1: U3.25 (SO1); also elsewhere on the board
/MCU/BR_SO2: U3.26 (SO2); also elsewhere on the board
/MCU/DC_CAL: U3.12 (DC_CAL); also elsewhere on the board
/MCU/EN_GATE: U3.16 (EN_GATE); also elsewhere on the board
/MCU/FAULT: U3.6 (FAULT); also elsewhere on the board
/MCU/H1: U3.17 (INH_A); also elsewhere on the board
/MCU/H2: U3.19 (INH_B); also elsewhere on the board
/MCU/H3: U3.21 (INH_C); also elsewhere on the board
/MCU/L1: U3.18 (INL_A); also elsewhere on the board
/MCU/L2: U3.20 (INL_B); also elsewhere on the board
/MCU/L3: U3.22 (INL_C); also elsewhere on the board
/MCU/SENS1: R23.2, R24.2; also elsewhere on the board
/MCU/SENS2: R26.2, R27.2; also elsewhere on the board
/MCU/SENS3: R32.2, R33.2; also elsewhere on the board
/Mosfet driver/H1_LOW: R50.1, U3.44 (SL_A); also elsewhere on the board
/Mosfet driver/H1_VS: C28.1, R32.1, U3.46 (SH_A); also elsewhere on the board
/Mosfet driver/H2_VS: C29.1, R26.1, U3.41 (SH_B); also elsewhere on the board
/Mosfet driver/H3_LOW: R48.1, U3.34 (SL_C); also elsewhere on the board
/Mosfet driver/H3_VS: C30.1, R23.1, U3.36 (SH_C); also elsewhere on the board
/Mosfet driver/M_H1: U3.47 (GH_A); also elsewhere on the board
/Mosfet driver/M_H2: U3.42 (GH_B); also elsewhere on the board
/Mosfet driver/M_H3: U3.37 (GH_C); also elsewhere on the board
/Mosfet driver/M_L1: U3.45 (GL_A); also elsewhere on the board
/Mosfet driver/M_L2: U3.40 (GL_B); also elsewhere on the board
/Mosfet driver/M_L3: U3.35 (GL_C); also elsewhere on the board
GND: C1.1, C8.1, C9.1, C18.2, C19.1, C20.1, C21.1, C23.1, C24.2, C25.2, C26.2, C33.2, C37.1, C39.1, C40.1, C43.2, C44.2, C49.2, C51.1, C52.1, D4.1 (A), D5.2 (A), R18.2, R20.2, R21.1, R24.1, R25.1, R27.1, R33.1, R49.1, R51.1, U2.1 (GND), U3.8 (M_PWM), U3.10 (GAIN), U3.28 (AGND), U3.39 (SL_B), U3.57 (GND(POWER_PAD)); also elsewhere on the board
unnamed: C18.1, C26.1, U3.13 (GVDD)
unnamed: C19.2, R19.2, U3.2 (COMP)
unnamed: C20.2, C52.2, U3.11 (OC_ADJ), U3.23 (DVDD)
unnamed: C21.2, R19.1
unnamed: C22.1, U3.14 (CP1)
unnamed: C22.2, U3.15 (CP2)
unnamed: C23.2, U3.27 (AVDD)
unnamed: C27.1, D4.2 (K), L1.1, U3.50 (PH), U3.51 (PH)
unnamed: C27.2, U3.52 (BST_BK)
unnamed: C28.2, U3.48 (BST_A)
unnamed: C29.2, U3.43 (BST_B)
unnamed: C30.2, U3.38 (BST_C)
unnamed: C34.1, R48.2, U3.33 (SN1)
unnamed: C34.2, R49.2, U3.32 (SP1)
unnamed: C36.1, R50.2, U3.31 (SN2)
unnamed: C36.2, R51.2, U3.30 (SP2)
unnamed: R17.2, R18.1, U3.3 (VSENSE)
unnamed: R20.1, U3.7 (DTC)
unnamed: R21.2, U3.1 (RT_CLK)
unnamed: R25.2, U3.49 (BIAS)
VCC: C24.1, C25.1, U2.2 (VO), U3.9 (M_OC), U3.24 (REF); also elsewhere on the board
V_SUPPLY: C1.2, C8.2, C9.2, C37.2, C39.2, C40.2, C43.1, C44.1, C49.1, C51.2, U3.29 (PVDD1), U3.53 (PVDD2), U3.54 (PVDD2); also elsewhere on the board

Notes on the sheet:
MCU must sense the voltage at each phase
3.3v regulator for the logic

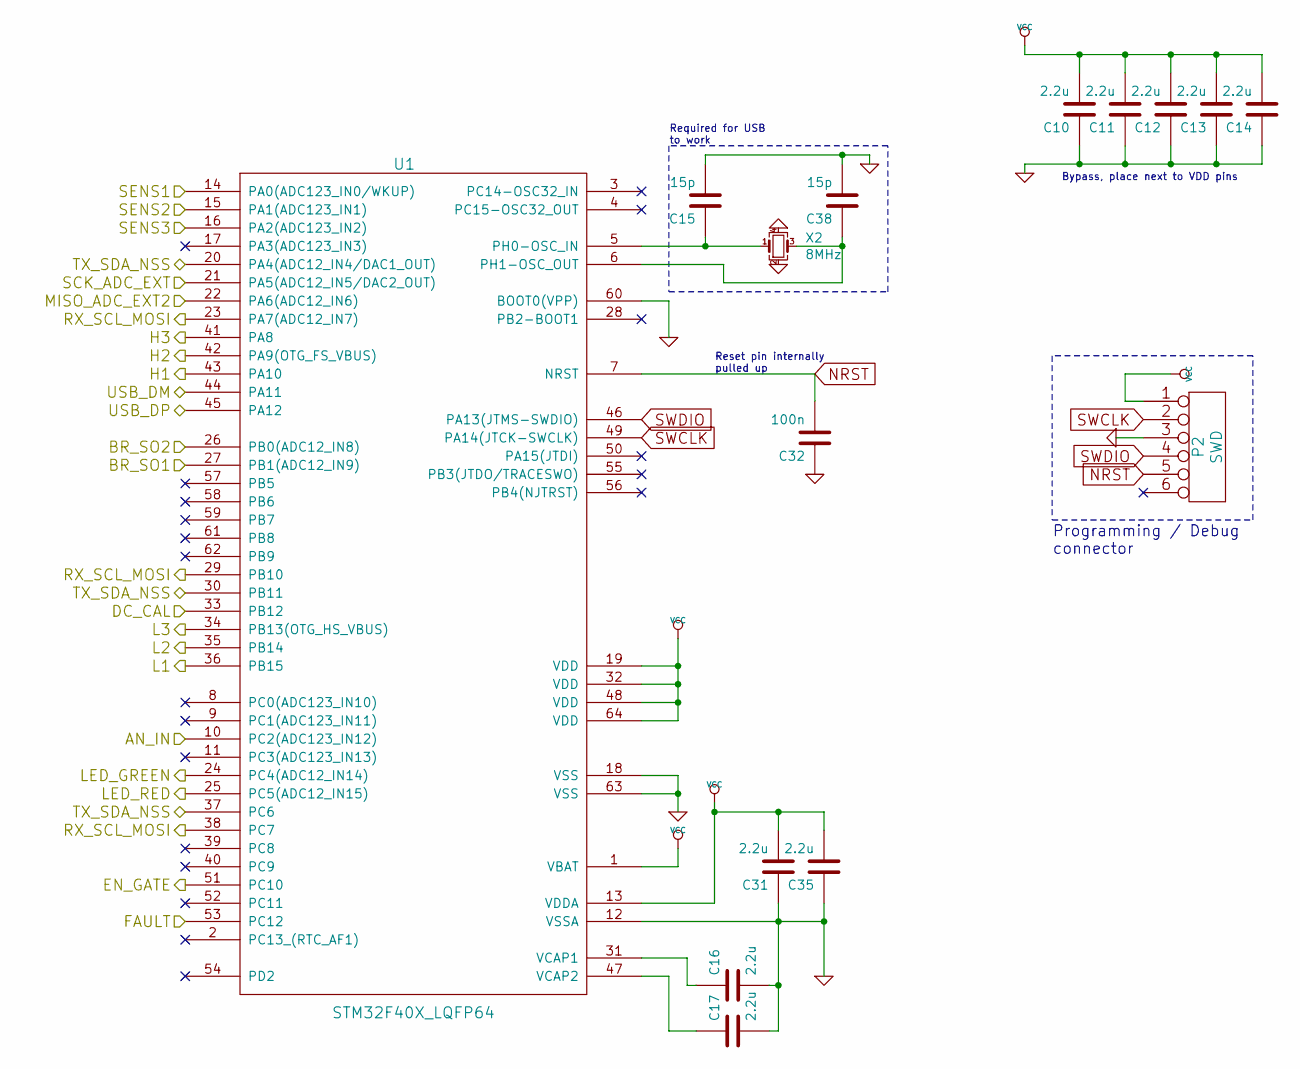
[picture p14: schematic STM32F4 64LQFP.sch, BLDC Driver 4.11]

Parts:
C10, C11, C12, C13, C14, C16, C17, C31, C35: 2.2u; C_0603_1608Metric
C15, C38: 15p; C_0603_1608Metric
C32: 100n; C_0603_1608Metric
P2: SWD; JST_PH_B6B-PH-K_1x06_P2.00mm_Vertical
U1: STM32F40X_LQFP64; LQFP-64_10x10mm_P0.5mm
X2: 8MHz; Crystal_SMD_Abracon_ABM3B-4Pin_5.0x3.2mm

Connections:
/MCU/AN_IN: U1.10 (PC2(ADC123_IN12)); also elsewhere on the board
/MCU/BR_SO1: U1.27 (PB1(ADC12_IN9)); also elsewhere on the board
/MCU/BR_SO2: U1.26 (PB0(ADC12_IN8)); also elsewhere on the board
/MCU/DC_CAL: U1.33 (PB12); also elsewhere on the board
/MCU/EN_GATE: U1.51 (PC10); also elsewhere on the board
/MCU/FAULT: U1.53 (PC12); also elsewhere on the board
/MCU/H1: U1.43 (PA10); also elsewhere on the board
/MCU/H2: U1.42 (PA9(OTG_FS_VBUS)); also elsewhere on the board
/MCU/H3: U1.41 (PA8); also elsewhere on the board
/MCU/L1: U1.36 (PB15); also elsewhere on the board
/MCU/L2: U1.35 (PB14); also elsewhere on the board
/MCU/L3: U1.34 (PB13(OTG_HS_VBUS)); also elsewhere on the board
/MCU/LED_GREEN: U1.24 (PC4(ADC12_IN14)); also elsewhere on the board
/MCU/LED_RED: U1.25 (PC5(ADC12_IN15)); also elsewhere on the board
/MCU/SENS1: U1.14 (PA0(ADC123_IN0/WKUP)); also elsewhere on the board
/MCU/SENS2: U1.15 (PA1(ADC123_IN1)); also elsewhere on the board
/MCU/SENS3: U1.16 (PA2(ADC123_IN2)); also elsewhere on the board
/MCU/USB_DM: U1.44 (PA11); also elsewhere on the board
/MCU/USB_DP: U1.45 (PA12); also elsewhere on the board
/MISO_RX_SCL: U1.22 (PA6(ADC12_IN6)); also elsewhere on the board
/RX_SCL_MOSI: U1.23 (PA7(ADC12_IN7)), U1.29 (PB10), U1.38 (PC7); also elsewhere on the board
/SCK_ADC_EXT: U1.21 (PA5(ADC12_IN5/DAC2_OUT)); also elsewhere on the board
/TX_SDA: U1.20 (PA4(ADC12_IN4/DAC1_OUT)), U1.30 (PB11), U1.37 (PC6); also elsewhere on the board
GND: C10.1, C11.1, C12.1, C13.1, C14.1, C15.2, C16.2, C17.2, C31.1, C32.1, C35.1, C38.2, P2.3, U1.12 (VSSA), U1.18 (VSS), U1.60 (BOOT0(VPP)), U1.63 (VSS), X2.2, X2.4; also elsewhere on the board
NRST: C32.2, P2.5, U1.7 (NRST)
unnamed: C15.1, U1.5 (PH0-OSC_IN), X2.1
unnamed: C16.1, U1.31 (VCAP1)
unnamed: C17.1, U1.47 (VCAP2)
unnamed: C38.1, U1.6 (PH1-OSC_OUT), X2.3
SWCLK: P2.2, U1.49 (PA14(JTCK-SWCLK))
SWDIO: P2.4, U1.46 (PA13(JTMS-SWDIO))
VCC: C10.2, C11.2, C12.2, C13.2, C14.2, C31.2, C35.2, P2.1, U1.1 (VBAT), U1.13 (VDDA), U1.19 (VDD), U1.32 (VDD), U1.48 (VDD), U1.64 (VDD); also elsewhere on the board

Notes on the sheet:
Programming / Debug connector
Reset pin internally pulled up
Required for USB to work
Bypass, place next to VDD pins

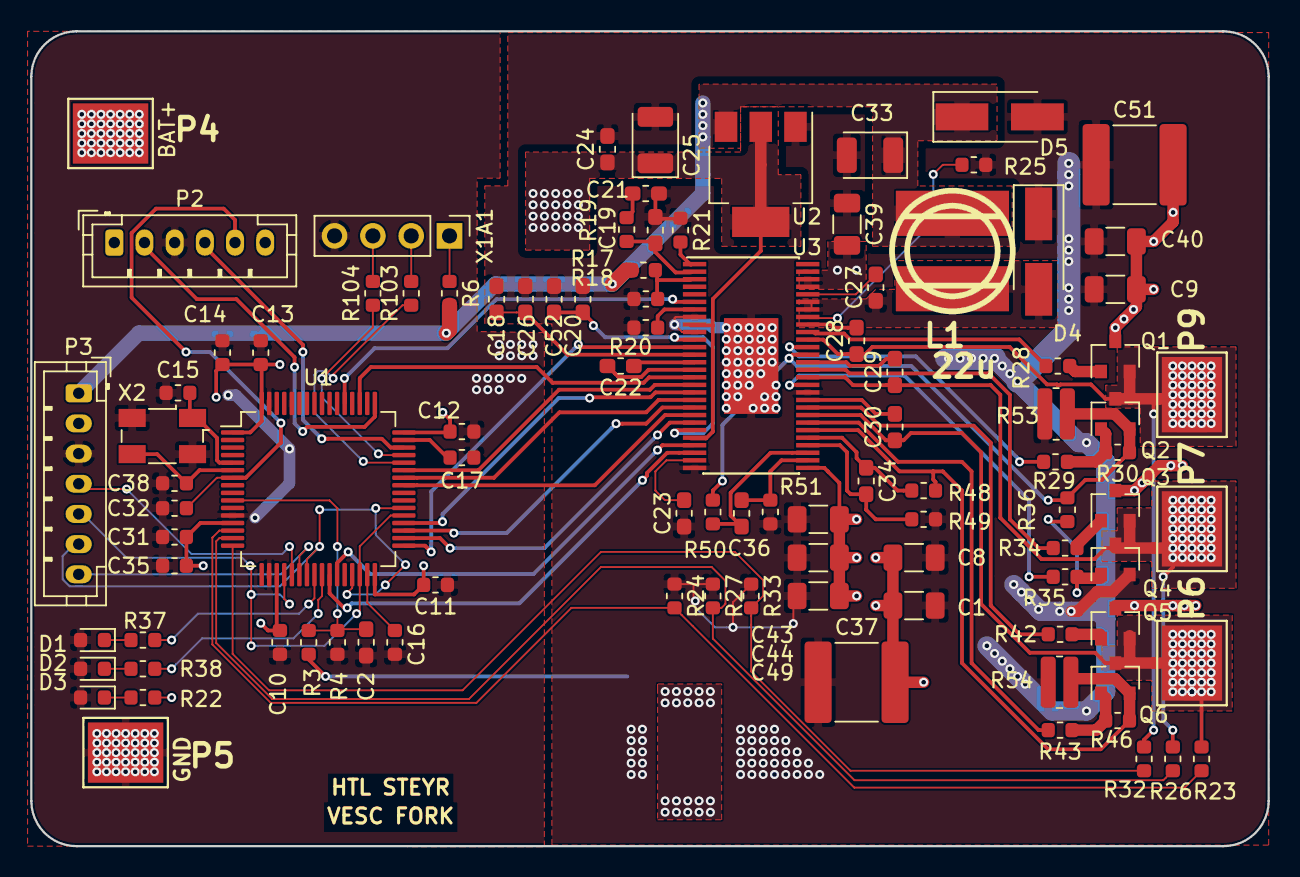
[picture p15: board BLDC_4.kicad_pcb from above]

Board: 2 copper layers, 82.0 x 54.0 mm, 99 parts (0 on the bottom side), 77 nets.

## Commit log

2019-11-08 Version 0.1 :godmode:
    [BLDC_4-2019-10-11-08-09-38.sch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]
2019-11-15 Removing and Redoing almost all auxilliary files
    Good ol' Benjamin made a lot of niftly little side files to make the schematic and layout easier to view. Things like pdfs and the like. The ones we still needed were kept and changed, the rest were 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
    [CAN.sch, hall_filters.sch, temp.sch]
2019-11-15 Fixing ERC Errors :+1:
    Turns out you need to mark pins as not connected. Who knew? Not me :sunglasses:
    [BLDC_4.kicad_pcb, STM32F4 64LQFP.sch]
2019-11-15 Nailing down the connecting pads with vias and Connecting the Filter Caps better
    Turns out you CAN put lipstick on a pig :+1:
    [BLDC_4.kicad_pcb]
2019-11-15 Reworked Silkscreen :suspect:
    It no longer looks like a pile of :shit:
    [BLDC_4.kicad_pcb]
2019-11-15 Rounded Corners on the PCB to take the edge of things
    :see_no_evil:
    [BLDC_4.kicad_pcb]
2019-11-19 Removed trash backup folder
    [BLDC_4-2019-10-11-08-09-38.sch, CAN-2019-10-11-08-09-38.sch, Power-2019-10-11-08-09-38.sch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]
2019-11-29 tiny silkscreen change
    [BLDC_4.kicad_pcb]
2019-11-29 Increasing current carrying capability
    Added more vias and dedicated polygons to output stage.
    [BLDC_4.kicad_pcb, STM32F4 64LQFP.sch]
2019-11-29 widened thermals
    [BLDC_4.kicad_pcb]
2019-12-06 Strengthening fills for output stage. Adding GND Fill
    More to come :godmode:
    [BLDC_4.kicad_pcb, BLDC_4.sch]
2019-12-13 Rework Board to fatten up supply
    :snake: sneaky stuff :snake:
    [BLDC_4.kicad_pcb, STM32F4 64LQFP.sch]
2019-12-13 Infill change
    [BLDC_4.kicad_pcb]
2020-01-10 Added BOM and reworked component naming to be inline with old VESC names
    :^)
    [BLDC4.12_BOM.ods, BLDC4.12_BOM_low_power.xlsx, BLDC_4.sch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]
2020-02-14 Fixed Crystal connection and footprint
    [BLDC_4.kicad_pcb, STM32F4 64LQFP.sch]
2020-03-13 v0.2 Bug fixes and improvements
    Fixed wrong GND net near shunts
    Seperated GND and PWRGND
    Added another GND net for capacitors near output stage
    [BLDC_4.kicad_pcb]
2020-03-13 fixes silkscreen. Updated Gerber
    [BLDC_4-B_Cu.gbr, BLDC_4-B_Mask.gbr, BLDC_4-B_SilkS.gbr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]
2020-03-13 Updated BOM
    [BLDC4.12_BOM_low_power.xlsx]
